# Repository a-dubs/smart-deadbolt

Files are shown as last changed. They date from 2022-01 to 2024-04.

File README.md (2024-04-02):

# Custom Smart Deadbolt 

Brainstormed, designed, built, and programmed a smart deadbolt from scratch

<br>

## Summary
- Attaches to my backdoor’s OEM deadbolt and turns the deadbolt lever to lock and unlock door
  - Mounts to the door and deadbolt without any adhesive or mounting hardware that could potentially damage the door
- Leverages radio modules for communication with smart home controller 
- Powered by an Arduino Pro Mini 5v that drives a high torque TT motor 
- Comprised of 13 different 3D-printed parts
  - Designed from scratch in Autodesk Inventor and 3D printed by yours truly
  - Custom modular design allows for rapid prototyping and iterative design 
- The deadbolt lever has a 3D-printed adapter that snaps around it (no adhesive necesssary) to convert it into one big gear 
  - This gear is then turned by the TT motor through a smaller gear with half the teeth which  
- Limit switch senses when door is closed or open - useful for functionality such as preventing deadbolt from being extended when trying to shut door
- Potentiometer sitting opposite the motor shaft provides two-fold functionality: 
  - Acts as an axle of sorts for the gear driven by the TT motor
  - Is a highly precise, non-volatile, axle "encoder" that allows for knowing the position of the deadbolt gear, and can thus infer when the deadbolt is turned into the unlocked or locked position
- Seamlessly integrates with my custom smart home ecosystem
- Functionality provided by Smart Home:
  - Automatically locks deadbolt after a minute if it is left unlocked
  - Remote monitoring of whether door is ajar/open
  - Remote monitoring and control of the deadbolt from anywhere, enabling the ability to let guests into home remotely
  - Function that prevents deadbolt from locking for any reason - useful for when you want to step outside quickly without needing your keys or a smartphone 
- Currently on its **4th** major version (V4)
  - V1 was the proof of concept
  - V2 was a more complete prototype, with only small improvements over V2, mostly just improved modularity 
  - V3 saw the complete overhaul of the design into a proper enclosure with better modularity and better complexity
  - V4 took V3's complete design and cleaned up the aesthetics considerably, while adding fully realized modularity allowing for the addition of more attachments and sensors

<br>

## Image Gallery

### The Smart Deadbolt w/ Clear Window On
The Smart Deadbolt w/ Clear Window On
<br>

### The Smart Deadbolt in Action!
The Smart Deadbolt in Action
<br>

### 3D Model of Full Assembly (V4) - Clear Walls
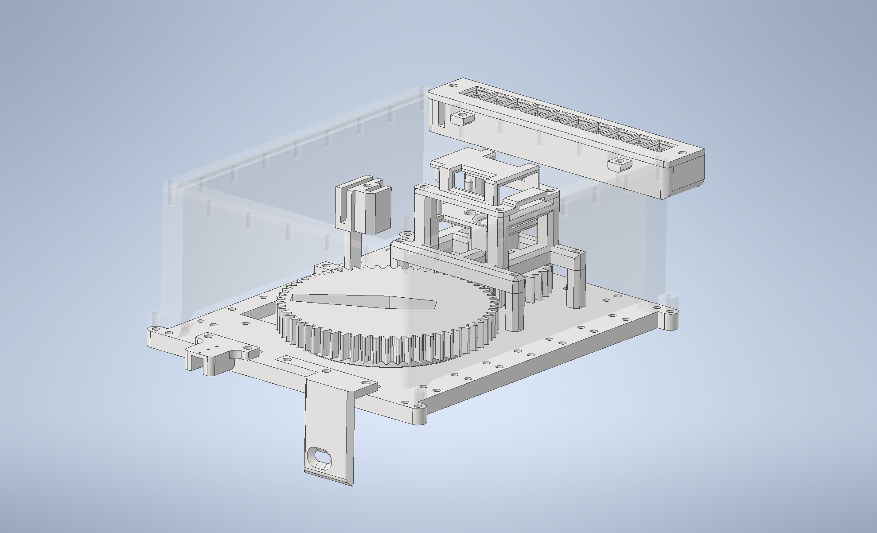
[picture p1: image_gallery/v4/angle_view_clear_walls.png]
3D Model of Full Assembly (V4) - Clear Walls

<br>

### 3D Model of Full Assembly (V4) - Opaque Walls
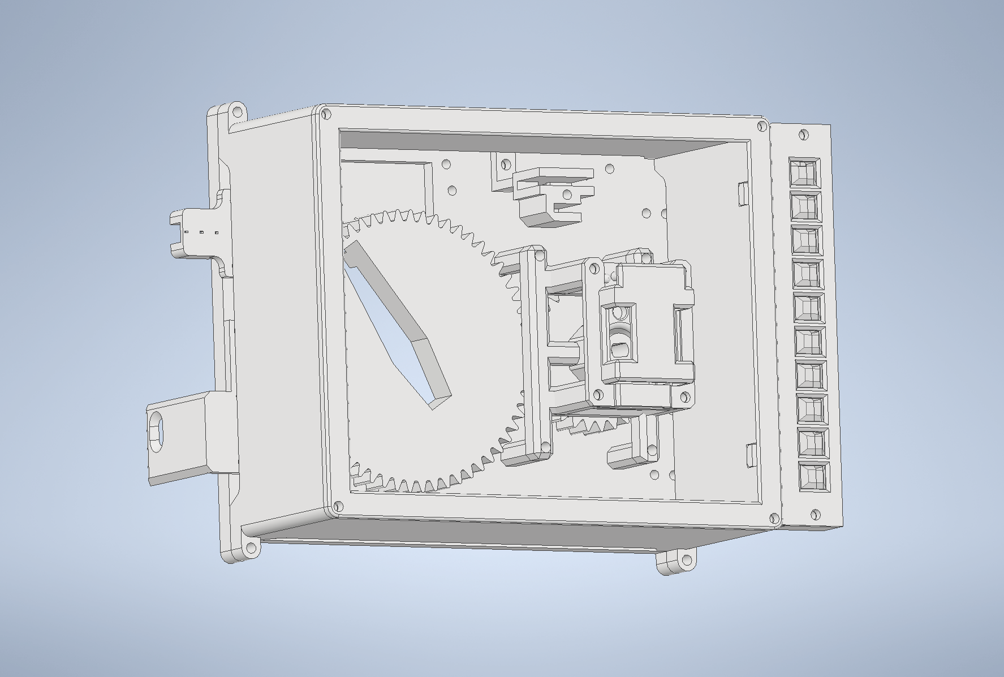
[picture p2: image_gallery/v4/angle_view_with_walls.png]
3D Model of Full Assembly (V4) - Opaque Walls

<br>

### 3D Model of Full Assembly (V4) - Front View
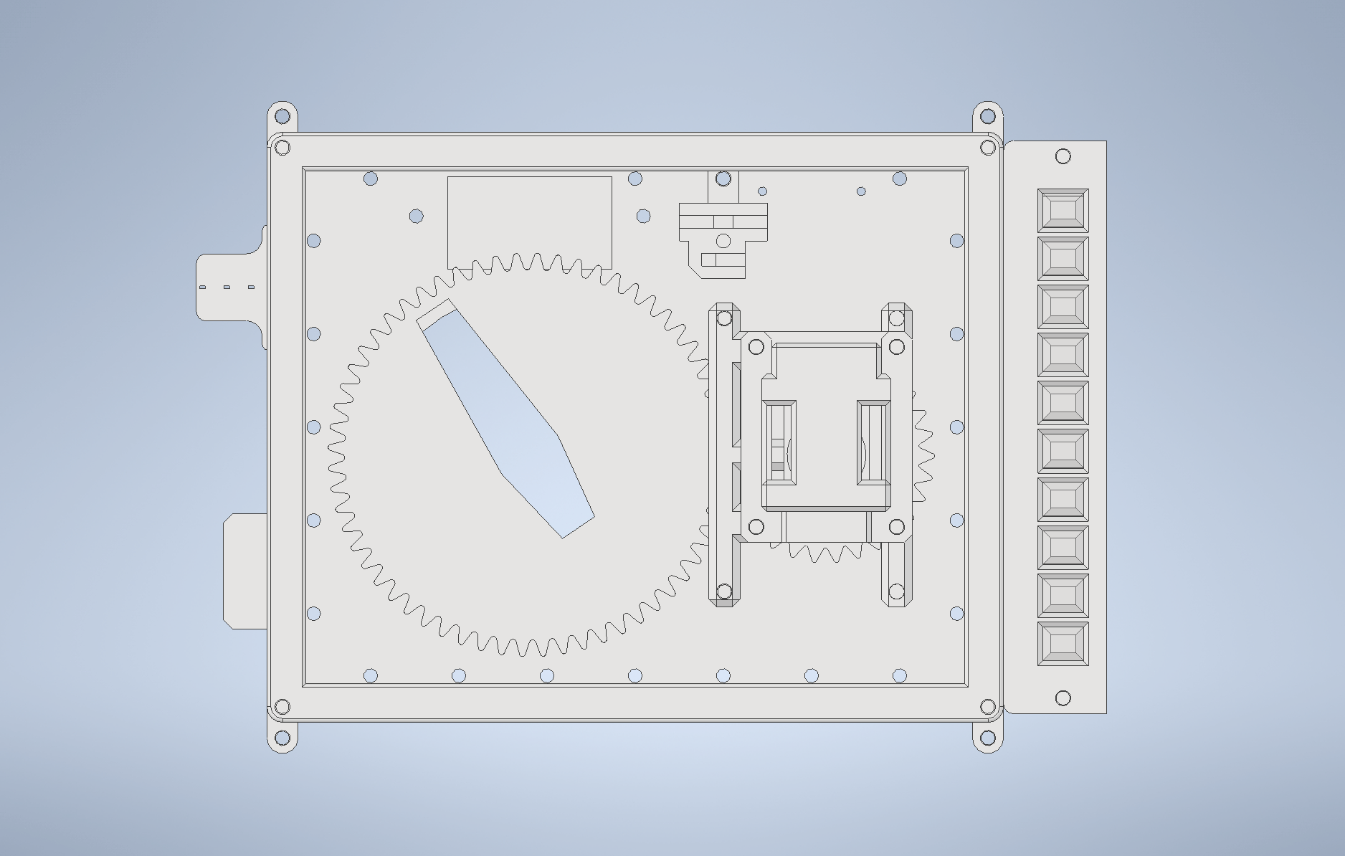
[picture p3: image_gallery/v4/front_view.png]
3D Model of Full Assembly (V4) - Front View

<br>

### OLDER VERSION (V3) - Exploded View of 3D Models 
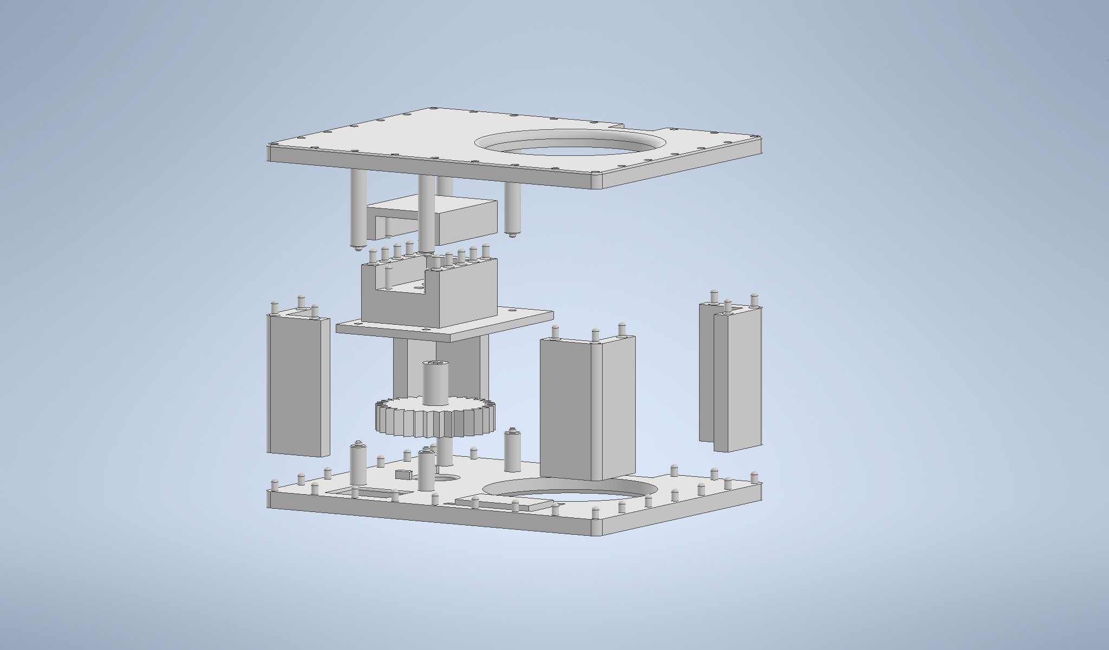
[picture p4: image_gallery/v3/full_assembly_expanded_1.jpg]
OLDER VERSION (V3) - Exploded View of 3D Models

<br>

<!--### Assembly of 3D Printed Components
![assembly of 3d printed components](https://github.com/a-dubs/smart-deadbolt/blob/master/image_gallery/full_assembly_1.jpg)

<br>

### Assembly of 3D Printed Components
![assembly of 3d printed components](https://github.com/a-dubs/smart-deadbolt/blob/master/image_gallery/full_assembly_2.jpg)

<br>

### View w/ Clear Sides
![view with clear sides](https://github.com/a-dubs/smart-deadbolt/blob/master/image_gallery/full_assembly_clear_sides_1.jpg)

<br>

### Exploded View
![exploded view](https://github.com/a-dubs/smart-deadbolt/blob/master/image_gallery/full_assembly_expanded_1.jpg)

<br>

### Exploded View w/ Clear Sides & Bottom
![exploded view with clears sides and bottom](https://github.com/a-dubs/smart-deadbolt/blob/master/image_gallery/full_assembly_expanded_2.jpg)

<br> -->

<br>

## Project Metadata

**Project Status** : Archived  
**Project Progress** : Functional  
**Project Dates** : Oct '21 - Aug '23  

<!-- portfolio.alecwarren.com position priority = 9 (-1 is lowest, 0 is default, 10 is highest) -->

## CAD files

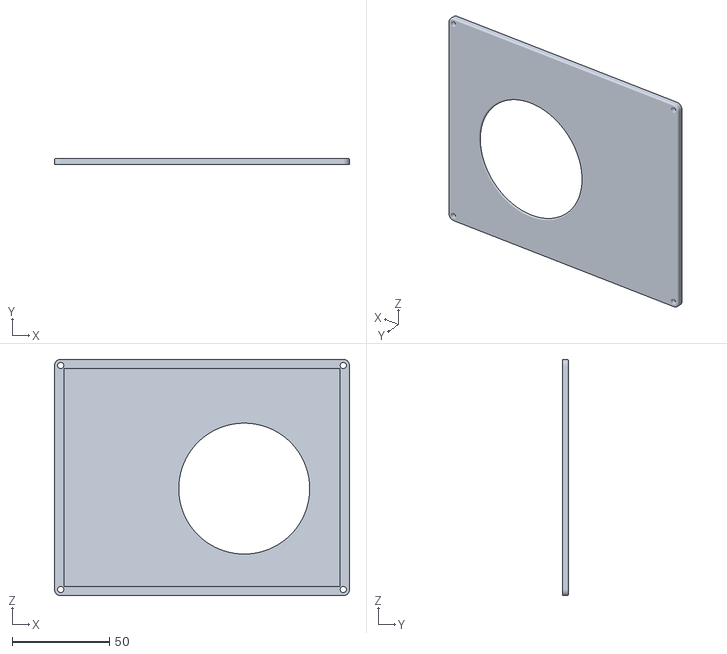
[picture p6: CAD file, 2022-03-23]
3D Modelling/door top plate with full window cutout.stl
151.5 x 3.20 x 121.4

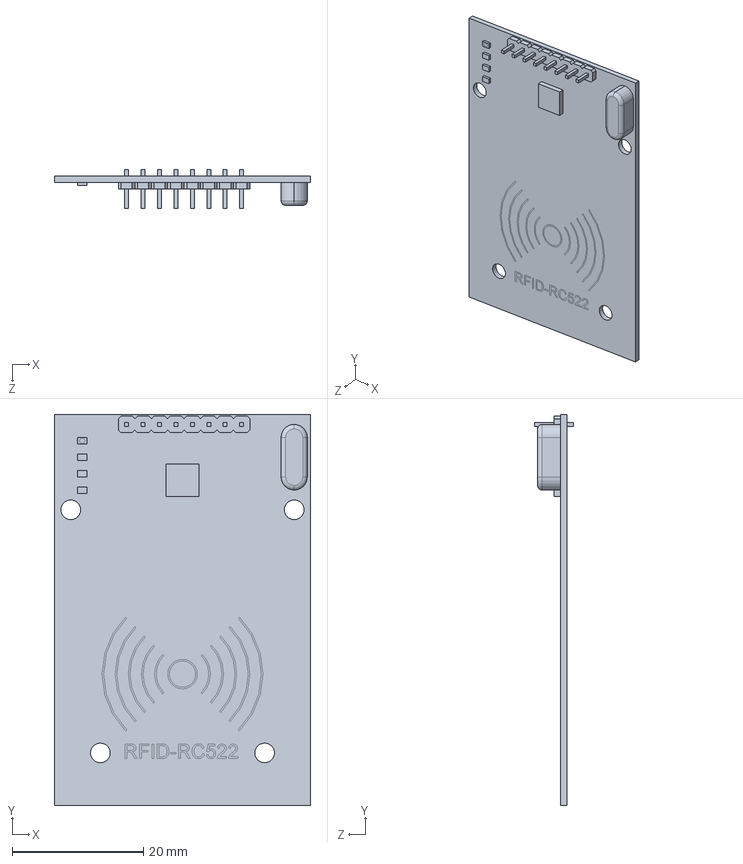
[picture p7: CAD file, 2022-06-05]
3D Modelling/downloaded/RFID-RC522 simple.SLDPRT
39.0 x 59.5 x 6.00 mm

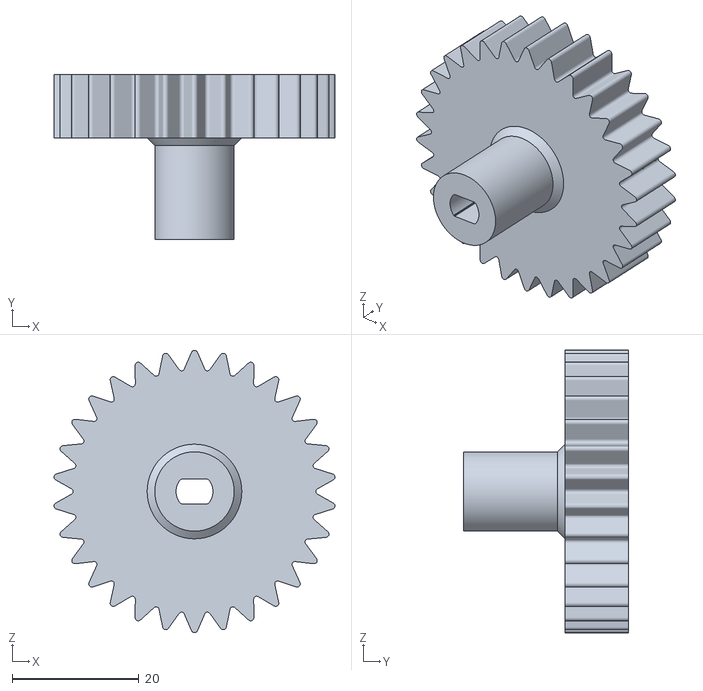
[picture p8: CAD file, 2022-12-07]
3D Modelling/motor gear.stl
44.3 x 26.0 x 44.5

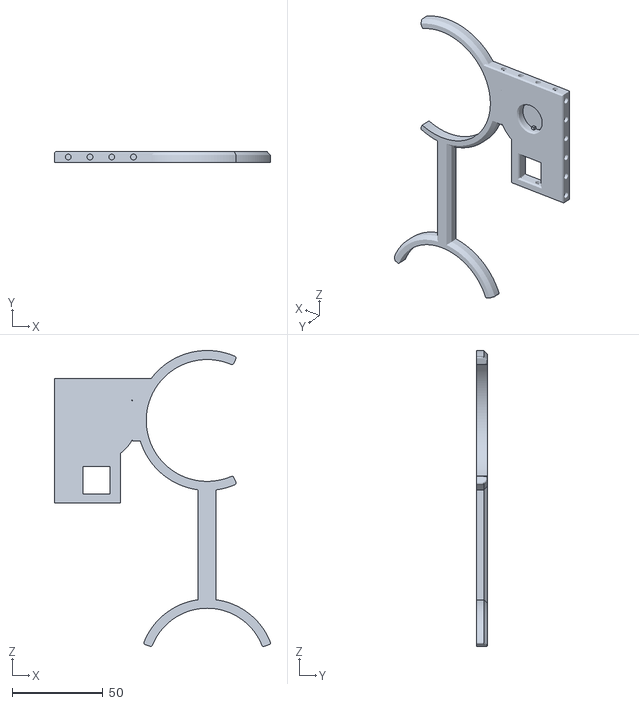
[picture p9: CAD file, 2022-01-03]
3D Modelling/proof of concepts (v1 - v2)/backplate with potentiometer.stl
119.2 x 6.00 x 163.3

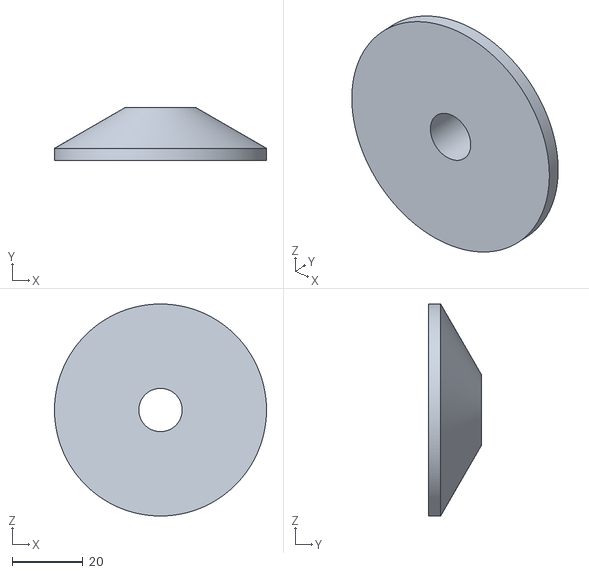
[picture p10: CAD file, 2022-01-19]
3D Modelling/proof of concepts (v1 - v2)/duplicate/driven gear addon.stl
60.0 x 15.0 x 60.0

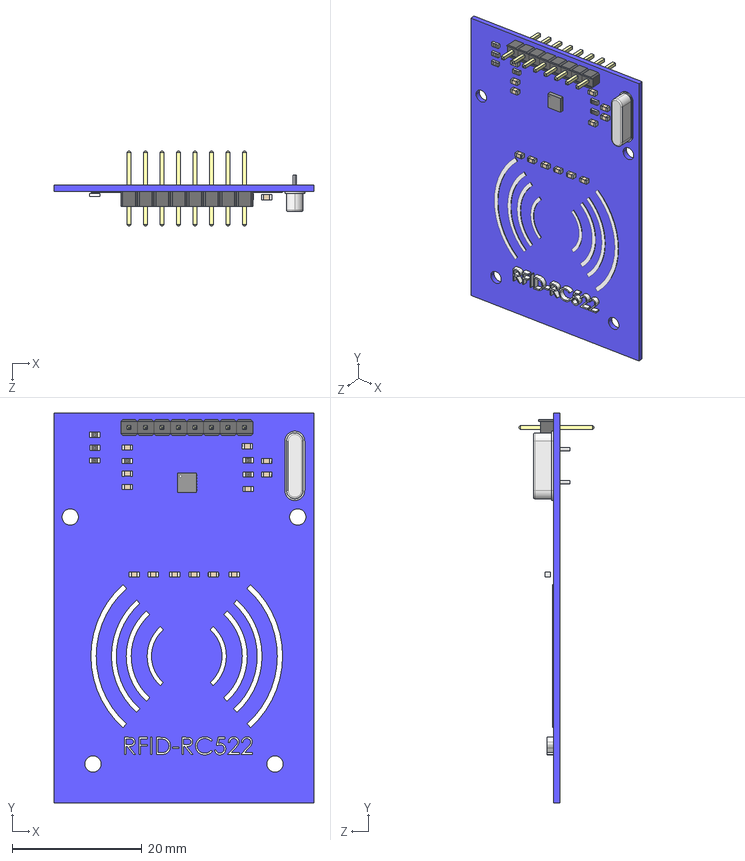
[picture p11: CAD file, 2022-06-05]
3D Modelling/downloaded/RFID.STEP
40.0 x 60.0 x 11.5 mm
User Library-S-PWSON-N12
User Library-Header_Male_8Pin
User Library-SMD Ceramic Capacitors_0603 (1608)_CH x 13

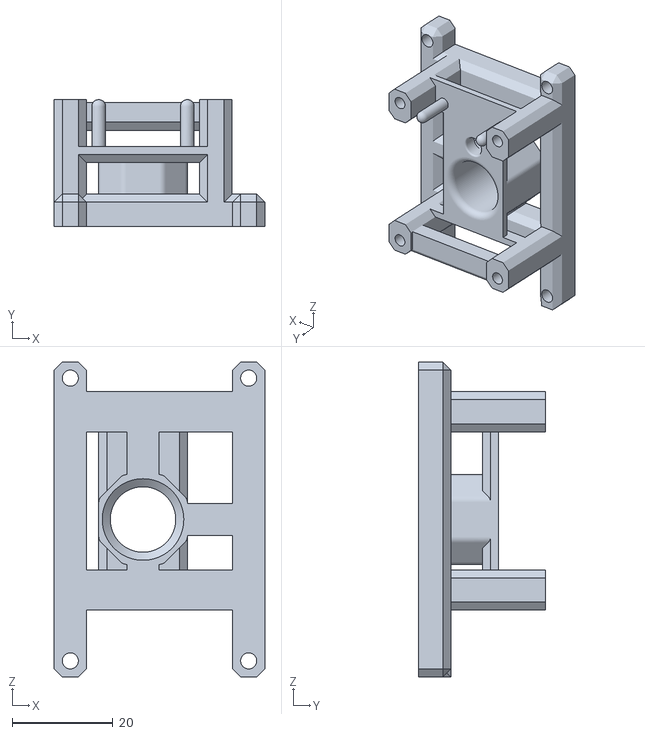
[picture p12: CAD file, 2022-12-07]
3D Modelling/motor mount plate.stl
41.9 x 25.2 x 62.6

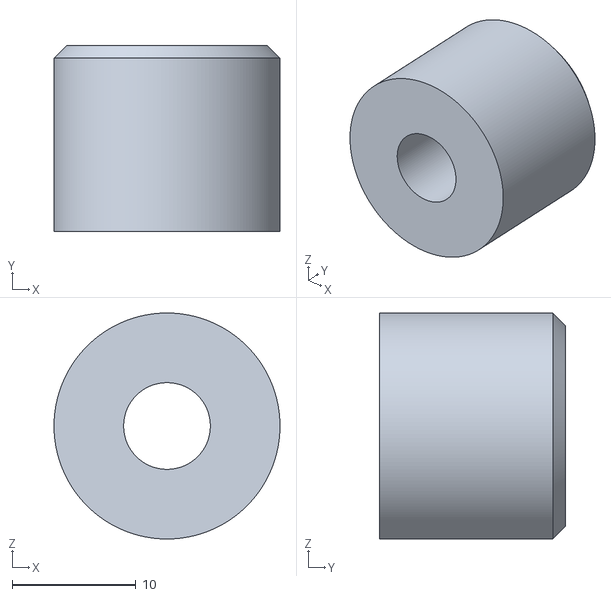
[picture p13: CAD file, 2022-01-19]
3D Modelling/proof of concepts (v1 - v2)/duplicate/driven gear spacer.stl
18.2 x 15.0 x 18.2

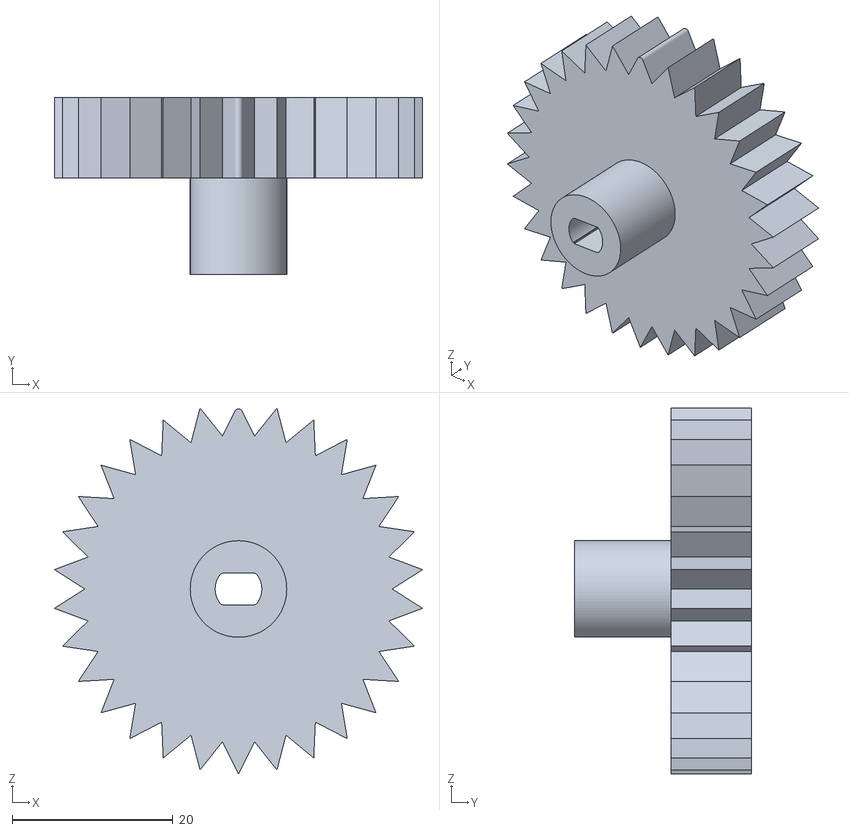
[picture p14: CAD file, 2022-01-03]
3D Modelling/proof of concepts (v1 - v2)/motor driven gear straight teeth for potentiometer.stl
45.7 x 22.0 x 45.5

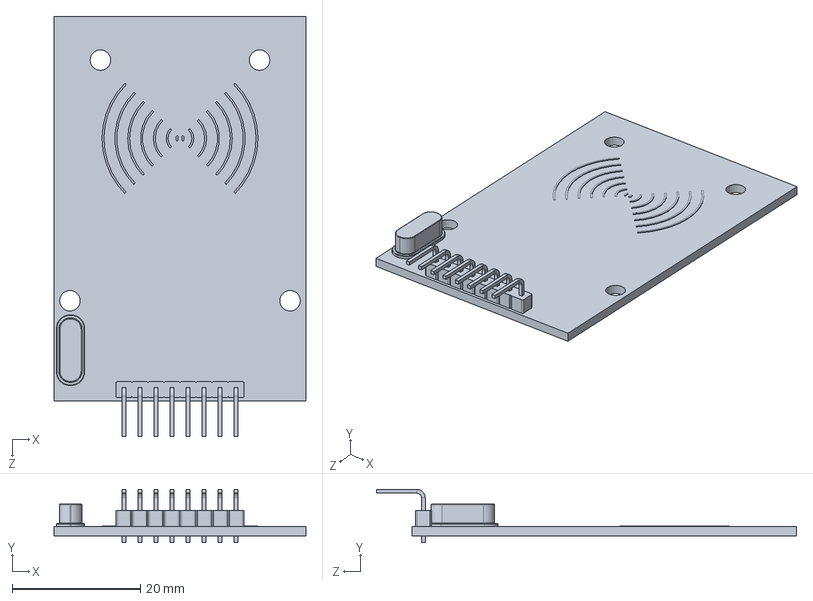
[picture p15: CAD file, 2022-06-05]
3D Modelling/downloaded/RC522.SLDPRT
39.2 x 8.30 x 65.5 mm

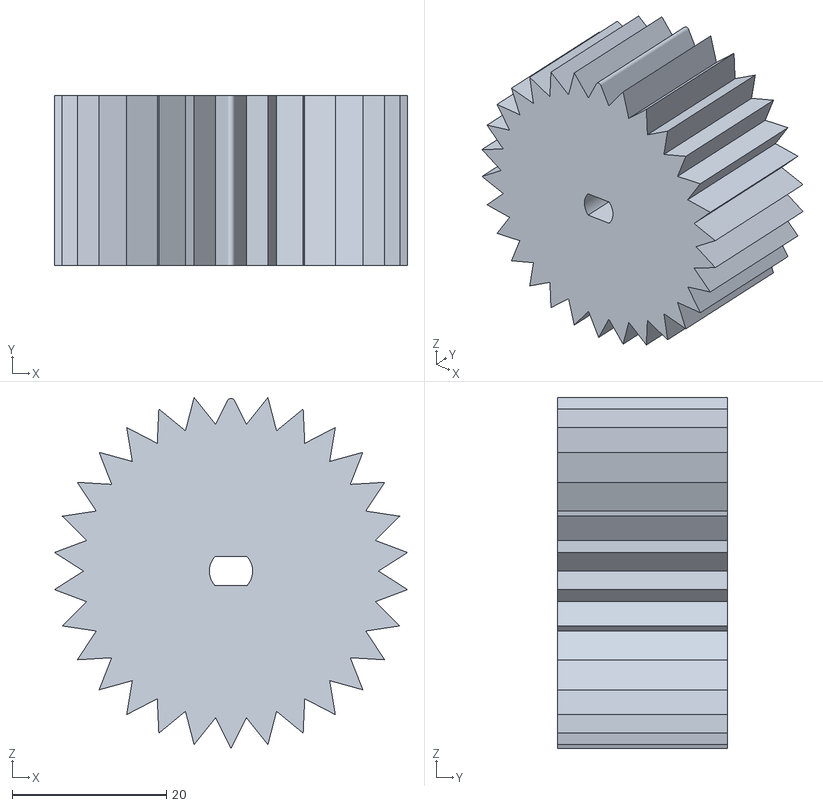
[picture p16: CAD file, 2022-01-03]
3D Modelling/proof of concepts (v1 - v2)/motor driven gear straight teeth for potentiometer tall.stl
45.7 x 22.0 x 45.5

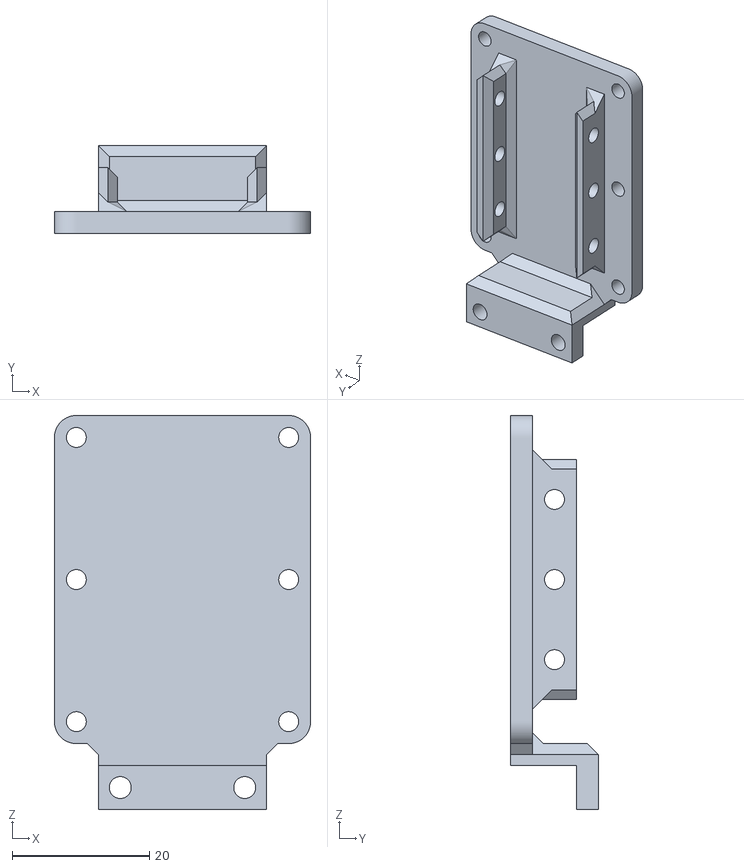
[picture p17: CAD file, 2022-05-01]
3D Modelling/auth arduino mount backplate.stl
37.3 x 12.8 x 57.4

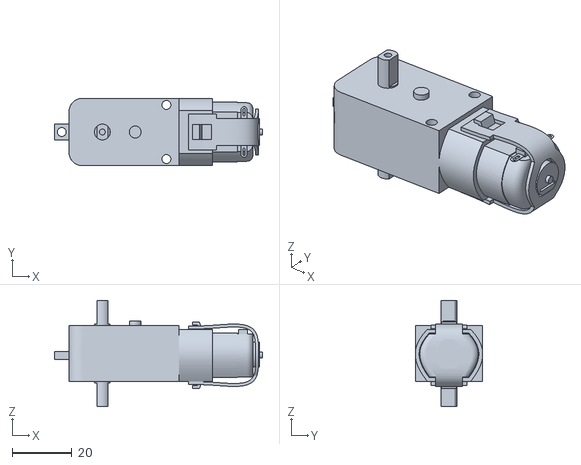
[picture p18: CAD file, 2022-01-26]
3D Modelling/downloaded/Yellow_Motor_Body.stl
69.7 x 22.6 x 35.6

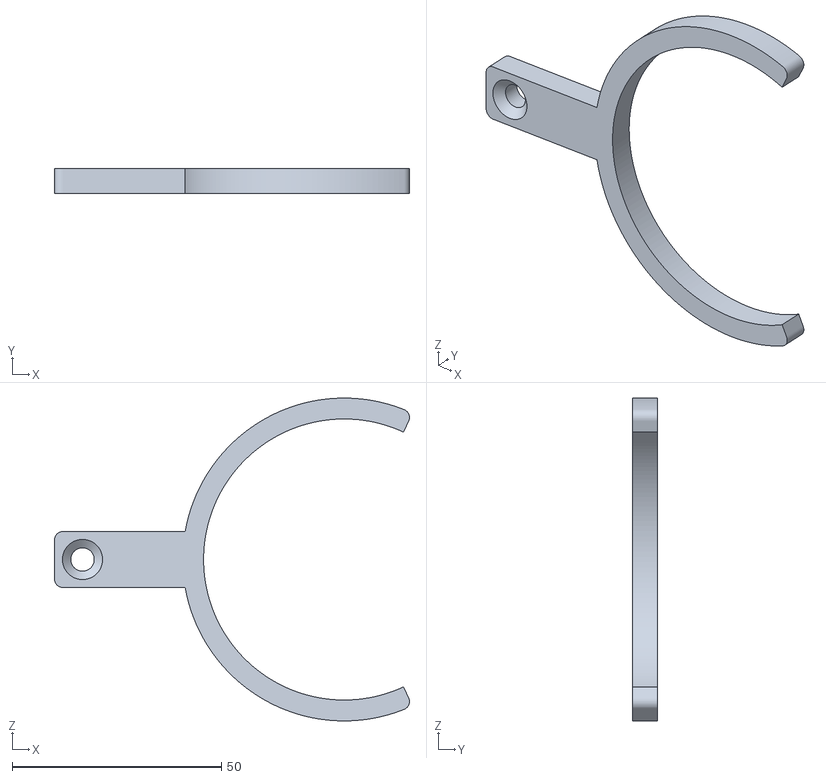
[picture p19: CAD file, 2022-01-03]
3D Modelling/proof of concepts (v1 - v2)/testing gear distances.stl
84.9 x 6.00 x 77.2

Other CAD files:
3D Modelling/power and ground splitter holders.stl
3D Modelling/proof of concepts (v1 - v2)/test attatchment.stl
3D Modelling/proof of concepts (v1 - v2)/backplate reinforcementipt.stl
3D Modelling/10x led strip grid divider opaque.stl
3D Modelling/10x led strip diffuser.ipt
3D Modelling/10x led strip grid divider opaque.ipt
3D Modelling/10x led strip holder .ipt
3D Modelling/10x led strip holder .stl
3D Modelling/10x led strip holder top cover.ipt
3D Modelling/10x led strip holder top cover.stl
3D Modelling/1x led strip diffuser.ipt
3D Modelling/1x led strip diffuser.stl
3D Modelling/OldVersions/10x led strip diffuser.0003.ipt
3D Modelling/OldVersions/10x led strip grid divider opaque.0005.ipt
3D Modelling/OldVersions/10x led strip holder .0009.ipt
3D Modelling/OldVersions/10x led strip holder top cover.0004.ipt
3D Modelling/OldVersions/1x led strip diffuser.0002.ipt
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

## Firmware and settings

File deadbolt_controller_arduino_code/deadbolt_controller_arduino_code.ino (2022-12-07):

#include <LibPrintf.h>
#include <Bounce2.h>
// #inc lude <SharpIR.h>
#include <FastLED.h>

#include <SoftwareSerial.h>

#undef RFID_ENABLED

#ifdef RFID_ENABLED
#include <SPI.h>
#include <MFRC522.h>
#endif
////////////////////////////////////////////////////////////////////////////////////////////////////
//////////////////////////////// Arduino Pro Mini Pinout Resrvations ///////////////////////////////
////////////////////////////////////////////////////////////////////////////////////////////////////

// [ TX   ]   Pin 0  -
// [ RX   ]   Pin 1  -
// [ INT  ]   Pin 2  - Limit Switch Digital Input
// [ INT  ] ~ Pin 3  - Deadbolt Toggle Button Digital Input
// [      ]   Pin 4  - 
// [      ] ~ Pin 5  - 
// [      ] ~ Pin 6  - 
// [      ]   Pin 7  - RF24 CE
// [      ]   Pin 8  - RF24 CS
// [      ] ~ Pin 9  - LED Strip Data Pin
// [ SS   ] ~ Pin 10 - 
// [ MOSI ] ~ Pin 11 - RF24
// [ MISO ]   Pin 12 - RF24
// [ SCK  ]   Pin 13 - RF24
// [      ]   Pin A0 - Motor Forward Digital Output
// [      ]   Pin A1 - Motor Backward Digital Output
// [      ]   Pin A2 - Motor Driver Sleep Digital Output (HIGH = Enable)
// [      ]   Pin A3 - Potentiometer Analog Input
// [      ]   Pin A4 - Ultrasonic Distance Sensor TRIG
// [      ]   Pin A5 - Ultrasonic Distance Sensor ECHO
// [      ]   Pin A6 -
// [      ]   Pin A7 -

#define MOTOR_FORWARD A0
#define MOTOR_BACKWARD A1
#define GEAR_POT A3
#define MOTOR_SLEEP A2
#define DOOR_LIMIT_SWITCH 2
// #define IR_DISTANCE_SENSOR
#define DEADBOLT_TOGGLE_BUTTON 3
#define ULTRASONIC_TRIG A4
#define ULTRASONIC_ECHO A5
#define LED_STRIP_DATA 9
#define MY_RF24_CE_PIN 7
#define MY_RF24_CS_PIN 8

////////////////////////////////////////////////////////////////////////////////////////////////////
////////////////////////////////////////////////////////////////////////////////////////////////////
////////////////////////////////////////////////////////////////////////////////////////////////////

//////////// MY SENSORS STUFF /////////////
// https://www.mysensors.org/download/sensor_api_20
// Enable debug prints
// #define MY_DEBUG
//#define MY_NODE_ID  2


// Enable and select radio type attached
#define MY_RADIO_RF24

#include <MySensors.h>

// MySensors Sensor & Actuator IDs
#define DEADBOLT_ID 30           // ID of the deadbolt actuator that unlocks/locks door
#define MOTDET_ID 31             // ID of the motion sensor for presence detection in LR
#define DOOR_ID 32               // ID of the door sensor for detecting whether door is ajar / has been opened

#define RFID_ID 37

// #define MOT_DET_PIN 2
// #define PERSON_PRESENT_PIN 5


#define LOCKED 1
#define UNLOCKED 0
#define SETUP_MODE 0
#define ULTRASONIC_TRIALS 1
#define LOCKED_POT_POS 220      // min value potentiometer must read for door to be "locked" (in degrees [0-270])
#define UNLOCKED_POT_POS 40      // max value potentiometer must read for door to be "unlocked" (in degrees [0-270])
#define MOTOR_MIN_OVERSHOOT 5    // how many degrees further than the minimum locked/unlocked potentiometer pos must the motor turn the deadbolt until stopping
#define MOTOR_STALL_TIMEOUT 200  // how many ms motor must be "stalled" for until it is considered officially stalled
#define MOTOR_STALL_DIST 1       // min number of degrees that must be advanced within the motor stall timeout window  for it to be considered officially stalled
#define HAND_PRESENT_MAX_DIST 50 // in cm
#define IR_MOTDET_TO ((unsigned long)60000)
#define HEARTBEAT_INTERVAL 1000              // in ms
#define MANUAL_ASSIST_ACTIVATION_THRESHOLD 5 // how many units out of 1024 potentiometer must turn before deadbolt motion is interpreted as the deadbolt being manually turned (>=)
#define KEEP_UNLOCKED_DUR 15000              // in ms, how long should deadbolt stay unlocked for before auto re-locking after being unlocked
#define DOOR_FULLY_OPEN_MIN_DUR 2000
#define MOTOR_MAX_TIME_ON 1000  // how long the motor can continuously run for before being considered stalled

#define ULTRASONIC_ENABLED false
// Bounce2::Button door_limit_switch_debouncer = Bounce2::Button();
//Bounce2::Button deadbolt_toggle_button = Bounce2::Button();
#ifdef RFID_ENABLED
MFRC522 mfrc522(RFID_SS_PIN, RFID_RST_PIN); // Create MFRC522 instance.
#endif
// SharpIR hand_distance_sensor(GP2Y0 A21YK0F_MODEL_CODE, IR_DISTANCE_SENSOR);

//////////////////////////////////////////////////
///////////////// FAST LED STUFF /////////////////
//////////////////////////////////////////////////

#define NUM_LEDS 8
CRGB leds[NUM_LEDS];
unsigned long leds_times_last_updated[NUM_LEDS];
#define TEMP_LEDS_DUR_ON 2000 

/*  DIAGNOSTIC LED STRIP COLOR CODE MEANINGS
+------------------------+-----------------------+
| Purpose                | Color Codes           |
+------------------------+-----------------------+
| Door State             | Red: Ajar             |
|                        | White: Shut           |
+------------------------+-----------------------+
| Deadbolt Current State | Green: Unlocked       |
|                        | Orange: Locked        |
+------------------------+-----------------------+
| Deadbolt Target State  | Green: Unlocked       |
|                        | Orange: Locked        |
+------------------------+-----------------------+
| Hand Detected          | Blue: Hand Detected   |
|                        | Off: Nothing Detected |
+------------------------+-----------------------+
| Authentication         | Red: RFID             |
|                        | Blue: Fingerprint     |
|                        | Off: None             |
+------------------------+-----------------------+
| Motor Warnings         | Red: Stalled          |
|                        | Off: None             |
+------------------------+-----------------------+
| Motor State            | Cyan: Motor on        |
|                        | Off: Motor off        |
+------------------------+-----------------------+
| Deadbolt Last Trigger  | HASS: Cyan            |
|                        | Auth: Magenta         |
|                        | Button: Red           |
|                        | Hand: Blue            |
+------------------------+-----------------------+
| RESERVED               | N/A                   |
+------------------------+-----------------------+
| RESERVED               | N/A                   |
+------------------------+-----------------------+
*/

#define MY_RED CRGB(255, 0, 0)
#define MY_GREEN CRGB(0, 200, 0)
#define MY_BLUE CRGB(0, 0, 200)
#define MY_CYAN CRGB(0, 200, 255)
#define MY_MAGENTA CRGB(255, 0, 200)
#define MY_ORANGE CRGB(150, 70, 0)
#define MY_WHITE CRGB(255, 255, 255)
#define MY_OFF CRGB(0,0,0)

#define DOOR_AJAR_COLOR MY_RED
#define DOOR_SHUT_COLOR MY_WHITE
#define DB_STATE_UNLOCKED_COLOR MY_GREEN
#define DB_STATE_LOCKED_COLOR MY_ORANGE
#define AUTH_RFID_COLOR MY_RED
#define AUTH_FINGERPRINT_COLOR MY_BLUE
#define AUTH_CONNECTED_COLOR MY_WHITE
#define AUTH_DISCONNECTED_COLOR MY_OFF
#define HAND_DET_COLOR MY_BLUE
#define HAND_NOT_DET_COLOR MY_OFF
#define MOTOR_WARN_STALL_COLOR MY_RED
#define MOTOR_WARN_NONE_COLOR MY_OFF
#define MOTOR_STATE_ON_COLOR MY_CYAN
#define MOTOR_STATE_OFF_COLOR MY_OFF 
#define TRIG_HASS_COLOR MY_CYAN
#define TRIG_AUTH_COLOR MY_MAGENTA
#define TRIG_BUTTON_COLOR MY_RED
#define TRIG_HAND_COLOR MY_BLUE


#define LEDS_DOOR_STATE 0
#define LEDS_DB_C_STATE 1 // CURRENT STATE
#define LEDS_DB_T_STATE 2 // TARGET STATE
#define LEDS_HAND_DET 3
#define LEDS_AUTH 4
#define LEDS_MOTOR_WARN 5
#define LEDS_MOTOR_STATE 6
#define LEDS_DB_LAST_TRIG 7
#define LEDS_RESERVED_1 8
#define LEDS_RESERVED_2 9

bool is_led_persistent[NUM_LEDS] = {
    true,    // LEDS_DOOR_STATE 0
    true,    // LEDS_DB_C_STATE 1 // CURRENT STATE
    true,    // LEDS_DB_T_STATE 2 // TARGET STATE
    true,    // LEDS_HAND_DET 3
    false,    // LEDS_AUTH 4
    false,    // LEDS_MOTOR_WARN 5
    true,    // LEDS_MOTOR_STATE 6
    false    // LEDS_DB_LAST_TRIG 7
    };

void set_led(int led_index, CRGB color)
{
    leds[led_index] = color;
    FastLED.show();
    leds_times_last_updated[led_index] = millis();
}

void check_to_clear_leds()
{
    for (int i=0; i < NUM_LEDS; i++)
    {
        if (!is_led_persistent[i] && leds[i] != MY_OFF && (millis() - leds_times_last_updated[i] > TEMP_LEDS_DUR_ON))
        {
            leds[i] = MY_OFF;
            printf("turned off led at index %d\n", i);
            FastLED.show();
        }
    }
    
}

void set_led_strip(CRGB color)
{
    fill_solid(&(leds[0]), NUM_LEDS, color);
    FastLED.show();
}

//////////////////////////////////////////////////
//////////////////////////////////////////////////
//////////////////////////////////////////////////


unsigned long last_time_heartbeat = 0;
unsigned long last_time_hand_detected = 0;
unsigned long last_time_door_closed = 0;
unsigned long last_time_door_opened = 0;
unsigned long last_time_unlocked = 0;
unsigned long last_time_present = 0;
unsigned long time_motor_started = 0;
unsigned long last_time_pot_advanced = 0;
bool door_was_fully_opened = false;
bool person_present = false;
bool person_present_recent_val = false;
short gear_pot_rot = 0;
short new_gear_pot_rot = 0;
bool deadbolt_current_state = UNLOCKED;
bool deadbolt_target_state = UNLOCKED;
bool motor_on = false;
bool motor_stalled = false;
short gear_pot_val_when_stopped; // value read by potentiometer after deadbolt was finished being moved by motor [0-1024]
short gear_pot_val;
bool main_loop_entered = false;
bool door_open = false;
bool button_pressed = false;
bool door_limit_switch_pressed = false;
bool rfid_accepted = false;
unsigned int hand_distance = 1000; // in cm ; set to high starting value so nothing gets triggered at boot
unsigned long dur;                 // variable for the duration of sound wave travel
bool rfid_unlocking_enabled = true;
static unsigned long last_interrupt_time = 0;
unsigned long interrupt_time = millis();
unsigned long db_btn_press_count = 0;
bool db_toggle_btn_pressed = false;
bool keep_unlocked = false;
bool hass_only_ctrl = false;
bool btn_ctrl_en = true;
bool l_sw_ctrl_en = true; 


#define KEEP_UNLOCKED_ID 20
#define HASS_CTRL_ONLY_ID 21 
#define BTN_CTRL_ENABLED_ID 22
#define L_SW_CTRL_ENABLED_ID 23

MyMessage deadbolt_msg(DEADBOLT_ID, V_LOCK_STATUS);
MyMessage motdet_msg(MOTDET_ID, V_TRIPPED);
MyMessage door_msg(DOOR_ID, V_TRIPPED);
MyMessage keep_unlocked_msg(KEEP_UNLOCKED_ID, V_STATUS);
MyMessage hass_ctrl_only_msg(HASS_CTRL_ONLY_ID, V_STATUS);
MyMessage btn_ctrl_enabled_msg(BTN_CTRL_ENABLED_ID, V_STATUS);
MyMessage l_sw_ctrl_enabled_msg(L_SW_CTRL_ENABLED_ID, V_STATUS);

void before()
{
#ifdef RFID_ENABLED
    // Make sure MFRC is disabled from the SPI bus
    pinMode(RFID_SS_PIN, OUTPUT);
    digitalWrite(RFID_SS_PIN, HIGH);
#endif
}

void presentation()
{
    set_led_strip(MY_OFF);
    // Send the sketch version information to the gateway and Controller
    sendSketchInfo("Backdoor MySensors Node V3", "07-07-22");

    // Register all sensors to gw (they will be created as child devices)
    present(DEADBOLT_ID, S_LOCK);
    present(MOTDET_ID, S_MOTION);
    present(DOOR_ID, S_DOOR);
    present(KEEP_UNLOCKED_ID, S_BINARY);
    present(HASS_CTRL_ONLY_ID, S_BINARY);
    present(BTN_CTRL_ENABLED_ID, S_BINARY);
    present(L_SW_CTRL_ENABLED_ID, S_BINARY);
}

// receive message from Gateway for deadbolt motor
void receive(const MyMessage &msg)
{
    printf("Message received for sensor #%d\n", msg.getSensor());
    if (msg.getType() == V_LOCK_STATUS)
    {
        bool lock_status_recvd = !msg.getBool();  // 1 = unlocked for HASS type lock , so invert it
         printf("Message received for deadbolt!\n");
        // if received LOCK command
        // if (msg.getSensor() == RFID_ID)
        // {
        //   if (!lock_status_recvd) {printf("Access granted has been terminated by HASS!\n");}
        // }
        if (msg.getSensor() == DEADBOLT_ID)
        {
            set_led(LEDS_DB_LAST_TRIG, TRIG_HASS_COLOR);
            if (lock_status_recvd)
            {
                lockDeadbolt();
            }
            else
            {
                unlockDeadbolt();
            }
        }
               
        
    }
    else {
      printf("bool msg recv'd: %d\n", msg.getBool());
      bool bool_recvd = msg.getBool();
      if (msg.getSensor() == KEEP_UNLOCKED_ID) 
            keep_unlocked = bool_recvd;
      else if (msg.getSensor() == HASS_CTRL_ONLY_ID) 
            hass_only_ctrl = bool_recvd;
      else if (msg.getSensor() == BTN_CTRL_ENABLED_ID) 
            btn_ctrl_en = bool_recvd;
      else if (msg.getSensor() == L_SW_CTRL_ENABLED_ID) 
            l_sw_ctrl_en = bool_recvd;
    }
}

void unlockDeadbolt(void)
{
    // if not already unlocked
    //  if (gear_pot_rot > UNLOCKED_POT_POS)
    if (deadbolt_target_state != UNLOCKED || deadbolt_current_state != UNLOCKED)
    {
        // if deadbolt is not currently being unlocked by motor
        if (!motor_on || deadbolt_target_state != UNLOCKED)
        {
            motor_on = true;
            printf("Unlocking Deadbolt...\n");
            digitalWrite(MOTOR_BACKWARD, LOW);
            digitalWrite(MOTOR_FORWARD, HIGH);
            time_motor_started = millis();
            last_time_pot_advanced = millis();
            send(deadbolt_msg.set(deadbolt_target_state ? "0" : "1"));
            set_led(LEDS_MOTOR_STATE, MOTOR_STATE_ON_COLOR);
            set_led(LEDS_DB_T_STATE, DB_STATE_UNLOCKED_COLOR);
            set_led(LEDS_MOTOR_WARN, MOTOR_WARN_NONE_COLOR);
        }
        // make sure that deadbolt target state is updated to proper value
        deadbolt_target_state = UNLOCKED;
        last_time_unlocked = millis();
    }
    // deadbolt is already unlocked
    else
    {
        deadbolt_target_state = UNLOCKED;
        last_time_unlocked = millis();
        printf("unlockDeadbolt(): Deadbolt already unlocked!\n");
        stopDeadbolt();
        //  send(deadbolt_msg.set(deadbolt_target_state?"0":"1"));
    }
    set_led(LEDS_DB_T_STATE, DB_STATE_UNLOCKED_COLOR);
}
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
void loop()
{
    if (!main_loop_entered)
    {
        set_led(LEDS_HAND_DET, HAND_NOT_DET_COLOR);
      
        time_motor_started = millis();
        stopDeadbolt();
        door_limit_switch_pressed = digitalRead(DOOR_LIMIT_SWITCH) == LOW; 
        door_open = !door_limit_switch_pressed;
        // update limit switch debouncer
        //    door_limit_switch_debouncer.update();
        //    door_open = door_limit_switch_debouncer.read() != 0;
        // enable motor controller
        digitalWrite(MOTOR_SLEEP, HIGH);
        Serial.print("\n\n\n< ENTERED MAIN LOOP >\n\n\n");
        main_loop_entered = true;
        send(deadbolt_msg.set(deadbolt_current_state ? "0" : "1"));
        send(motdet_msg.set("0"));

        send(door_msg.set(door_open ? "1" : "0"));

        send( keep_unlocked_msg.set( keep_unlocked ? "1" : "0") );
        send( hass_ctrl_only_msg.set( hass_only_ctrl ? "1" : "0") );
        send( btn_ctrl_enabled_msg.set( btn_ctrl_en ? "1" : "0") );
        send( l_sw_ctrl_enabled_msg.set( l_sw_ctrl_en ? "1" : "0") );
        
    }

    //////////////////////////////////////
    // DEADBOLT CONTROL CODE //
    /////////////////////////////////////
    new_gear_pot_rot = (analogRead(GEAR_POT) * 270.0) / 1024.0;
    if ((deadbolt_target_state == LOCKED && new_gear_pot_rot > gear_pot_rot) || (deadbolt_target_state == UNLOCKED && new_gear_pot_rot < gear_pot_rot))
    {
        last_time_pot_advanced = millis();
    }

    gear_pot_rot = new_gear_pot_rot;
    gear_pot_val = analogRead(GEAR_POT);
    //  printf("gear potentiometer rotation [0-270deg]: %d ; raw value: %d\n", gear_pot_rot, gear_pot_val);
      // if deadbolt has been locked
      if (gear_pot_rot >= LOCKED_POT_POS)
      {
          if (deadbolt_current_state != LOCKED)
          {
              if (deadbolt_current_state == UNLOCKED)
              {
                  printf("Deadbolt is now locked\n");
              }

              deadbolt_current_state = LOCKED;
              stopDeadbolt();
          }
          if (motor_on && deadbolt_target_state == LOCKED)
          {
              stopDeadbolt();
          }
      }
      // if deadbolt has been unlocked
      else if (gear_pot_rot <= UNLOCKED_POT_POS)
      {
          if (deadbolt_current_state != UNLOCKED)
          {
              if (deadbolt_current_state == LOCKED)
              {
                  printf("Deadbolt is now unlocked\n");
                  
              }

              deadbolt_current_state = UNLOCKED;
              stopDeadbolt();
          }
          if (motor_on && deadbolt_target_state == UNLOCKED)
          {
              stopDeadbolt();
          }
      }

      // if motor has stalled
      if (motor_on && (millis() - last_time_pot_advanced >= MOTOR_STALL_TIMEOUT || millis() - time_motor_started > MOTOR_MAX_TIME_ON))
      {
          
          motor_stalled = true;
          set_led(LEDS_MOTOR_WARN, MOTOR_WARN_STALL_COLOR);
//          printf("MOTOR STALLED!\n");
          if (millis() - last_time_pot_advanced >= MOTOR_STALL_TIMEOUT)
          { 
            printf("motor stalled #1\n");
          }
          else if (millis() - time_motor_started > MOTOR_MAX_TIME_ON)
          {
            printf("motor stalled #2\n");
          }
          if (deadbolt_target_state == LOCKED)
          {
              unlockDeadbolt();
          }
          else
          {
              lockDeadbolt();
          }
      }

#ifdef RFID_ENABLED
      // activate rfid reader and run RFID scanner logic
      read_rfid();

      // if valid rfid device/tag presented then unlock the deadbolt
      if (rfid_accepted)
      {
          printf("deadbolt unlocked via RFID \n");
          rfid_accepted = false;
          unlockDeadbolt();
      }
#endif

      // update limit switch debouncer
      //      door_limit_switch_debouncer.update();

      // limit switch's state has changed
      //      if ( door_limit_switch_debouncer.changed() ) {
      //
      //        // if limit switch is NOT "pressed" ( == 0) then door has been opened
      //         door_open = door_limit_switch_debouncer.read() != 0;
      //
      //        // after old wire snapped, using normal closed wire instead now
      ////        door_open = door_limit_switch_debouncer.read() == 0;
      //        digitalWrite(DOOR_OPEN_LED, door_open);
      //        // send updated door state msg
      //        send(door_msg.set(door_open ? "1" : "0"));
      //
      //        // if door has just been opened
      //        if (door_open)
      //        {
      //          printf("Door was just opened!\n");
      //        }
      //        // if door has just been closed
      //        else
      //        {
      //          last_time_door_closed = millis();
      //          printf("Door was just closed!\n");
      //          lockDeadbolt();
      //        }
      //

      //      }


      if (door_limit_switch_pressed == door_open)
      {

          // if limit switch is NOT "pressed" ( == 0) then door has been opened
          door_open = !door_limit_switch_pressed;

          // after old wire snapped, using normal closed wire instead now
          //        door_open = door_limit_switch_debouncer.read() == 0;
          
          // send updated door state msg
          send(door_msg.set(door_open ? "1" : "0"));
          set_led(LEDS_DOOR_STATE, door_open ? DOOR_AJAR_COLOR : DOOR_SHUT_COLOR);
          // if door has just been opened
          if (door_open)
          {
              last_time_door_opened = millis();
              // if (last_time_hand_detected > 1000)
              if (!hass_only_ctrl && l_sw_ctrl_en && deadbolt_target_state == LOCKED && deadbolt_current_state != LOCKED)
              {
                  unlockDeadbolt();
                  set_led(LEDS_DB_LAST_TRIG, TRIG_HASS_COLOR);
              }
              printf("Door was just opened!\n");
          }
          // if door has just been closed
          else
          {
              last_time_door_closed = millis();
              printf("Door was just closed!\n");
              if (!hass_only_ctrl && !keep_unlocked && l_sw_ctrl_en)
              {
              lockDeadbolt();
              }
          }
      }

      
  if (digitalRead(DEADBOLT_TOGGLE_BUTTON) == LOW)
  {
    if(db_toggle_btn_pressed != !digitalRead(DEADBOLT_TOGGLE_BUTTON))
    {
      wait(10);
      if (digitalRead(DEADBOLT_TOGGLE_BUTTON) == LOW)
      {
        db_toggle_btn_pressed =  true; // invert it because its pulled HIGH so LOW means pressed
        printf("db toggle button pressed\n");
        if (!hass_only_ctrl && btn_ctrl_en)
        {
          if (deadbolt_target_state == LOCKED)
          unlockDeadbolt();
          else if(deadbolt_current_state == UNLOCKED)
          lockDeadbolt(); 
          set_led(LEDS_DB_LAST_TRIG, TRIG_BUTTON_COLOR);
        }
      }
    }
  }
  
  else if (db_toggle_btn_pressed == true) {
    wait(10);
    if (digitalRead(DEADBOLT_TOGGLE_BUTTON) == HIGH)
    {
      db_toggle_btn_pressed = false;
    }
  }
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

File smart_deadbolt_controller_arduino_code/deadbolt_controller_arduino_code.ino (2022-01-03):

#include <LibPrintf.h>

#define IR_MOT_DET_PIN 7
#define PERSON_PRESENT_PIN 3
#define RELAY3 10
#define MOTOR_FORWARD A0
#define MOTOR_BACKWARD A1
#define GEAR_POT A3
#define MOTOR_SLEEP A2

#define LOCKED 1
#define UNLOCKED 0

#define SETUP_MODE false

#define LOCKED_POT_POS 210 // min value potentiometer must read for door to be "locked" (in degrees [0-270])
#define UNLOCKED_POT_POS  20 // max value potentiometer must read for door to be "locked" (in degrees [0-270])
#define IR_MOTDET_TO ((unsigned long) 20000)


unsigned long last_time_present = 0;
bool person_present = false;
bool person_present_recent_val = false;
short gear_pot_pos = 0;
bool deadbolt_current_state = false;
bool deadbolt_target_state = true;
bool motor_on = false;

void unlockDeadbolt(void)
{
  deadbolt_target_state = UNLOCKED;
  motor_on = true;
//  printf("Unlocking Deadbolt...\n");
  digitalWrite(MOTOR_BACKWARD, HIGH);
  digitalWrite(MOTOR_FORWARD, LOW);
}


void lockDeadbolt(void)
{
  deadbolt_target_state = LOCKED;
  motor_on = true;
//  printf("Locking Deadbolt...\n");
  digitalWrite(MOTOR_BACKWARD, LOW);
  digitalWrite(MOTOR_FORWARD, HIGH);
}

void stopDeadbolt(void)
{
  motor_on = false;
//  printf("Stopping Deadbolt Motor...\n");
  digitalWrite(MOTOR_BACKWARD, LOW);
  digitalWrite(MOTOR_FORWARD, LOW);
}

void setup() {
  // put your setup code here, to run once:
  pinMode(IR_MOT_DET_PIN, INPUT);
  pinMode(PERSON_PRESENT_PIN, OUTPUT);
  pinMode(MOTOR_FORWARD, OUTPUT);
  pinMode(MOTOR_BACKWARD, OUTPUT);
  pinMode(MOTOR_SLEEP, OUTPUT);
  // init value of gear potentiometer position 

  // enable motor controller
  digitalWrite(MOTOR_SLEEP, HIGH);
  if (!SETUP_MODE)
  {
    attachInterrupt(digitalPinToInterrupt(IR_MOT_DET_PIN), presenceISR, RISING);
  }
  Serial.begin(115200);
}

void loop() {
 
    if (person_present_recent_val != person_present)
    {
      
      person_present ? Serial.println("Person is now present!") : Serial.println("Person is no longer present.");
//      person_present ? unlockDeadbolt() : lockDeadbolt();
    }
    person_present_recent_val = person_present;
    if (millis() - last_time_present > IR_MOTDET_TO)
    {
      person_present = false;
    }
    digitalWrite(PERSON_PRESENT_PIN, person_present);

  gear_pot_pos = (analogRead(GEAR_POT) * 270.0) / 1024.0;

  if (!SETUP_MODE)
  {
    if (gear_pot_pos >= LOCKED_POT_POS)
    {
//      deadbolt_current_state = LOCKED;
      if (deadbolt_current_state != LOCKED)
      {
        if (deadbolt_current_state)
        stopDeadbolt();
        printf("Deadbolt is now locked\n");
        deadbolt_current_state = LOCKED;
      }
    }
    else if (gear_pot_pos <= UNLOCKED_POT_POS)
    {
//      deadbolt_current_state = UNLOCKED;
      if (deadbolt_current_state != UNLOCKED)
      {
        printf("Deadbolt is now unlocked\n");
        deadbolt_current_state = UNLOCKED;
          
        stopDeadbolt();
      }
    }
  //  else if (gear_pot_pos > UNLOCKED_POT_POS && gear_pot_pos < LOCKED_POT_POS){
  ////    if (deadboltCurrentState != MOVING)
  ////    {
  ////      printf("Deadbolt is now moving!\n");
  ////      deadboltCurrentState == MOVING;
  ////    }
  //  }

  }  
//
//  static volatile short new_deadbolt_pot_pos =  (analogRead(GEAR_POT) * 270.0) / 1024.0;
//  if ((new_deadbolt_pot_pos - gear_pot_pos > 1) || (new_deadbolt_pot_pos - gear_pot_pos < -1))
//  {
//    printf("gear potentiometer position [0-270deg] %d:\n", new_deadbolt_pot_pos); 
//  }
//  gear_pot_pos = new_deadbolt_pot_pos;
////  printf("raw potentiometer value [0-1024]: %ld\n", analogRead(GEAR_POT));
// 
//  printf("%d, %d\n", deadboltCurrentState, deadboltTargetState);
//  if (deadboltCurrentState != deadboltTargetState && deadboltCurrentState != MOVING)
//  {
//    if (deadboltTargetState == LOCKED)
//    {
//      lockDeadbolt();
//    }
//    else if (deadboltTargetState == UNLOCKED)
//    {
//      unlockDeadbolt();
//    }
//    else {
//      stopDeadbolt();
//    }
//  }
//
//
//  
  if (Serial.available() > 0)
  {
    char ui = Serial.read();
    if (ui == 's')
    {
      stopDeadbolt();
    }
    else if (ui == 'u')
    {
      unlockDeadbolt();
    }
    else if (ui == 'l')
    {
      lockDeadbolt();
    }
    else if (ui == 'p')
    {
      printf("gear potentiometer position [0-270deg] %d:\n", gear_pot_pos);
    }
    else if (ui == 'd')
    {
      printf("Deadbolt is currently %s!\n", deadbolt_current_state == LOCKED ? "locked" : "unlocked");
      printf("Deadbolt's target state is %s!\n", deadbolt_target_state == LOCKED ? "locked" : "unlocked");
      printf("Deadbolt is currently %s!\n", motor_on == true ? "moving" : "stopped");
    }
  }
  delay(10);
//  
//
//  
//
//
//  
//  
// 
//  

}

void presenceISR(void)
{
 
    Serial.println("Presence detected");
  person_present = true;
  last_time_present = millis();
    digitalWrite(PERSON_PRESENT_PIN, HIGH);
}

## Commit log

2022-01-03 v1.0.0 Merged arduino code & 3d models into repo
    [TT motor attach to linear motion gear adapter.0008.ipt, TT motor attach to linear motion gear adapter.ipt, TT motor attach to linear motion gear adapter.stl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]
2022-01-19 v1.0.1 tweaked top of enclosure and standoffs
    [deadbolt enclosure top with window for deadbolt.0002.ipt, deadbolt enclosure top with window for deadbolt.ipt, deadbolt enclosure top with window for deadbolt.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]
2022-01-24 v3.0.0 fixed B2MCS, widened motor plate standoffs
    [door backplate.0015.ipt, door backplate.0018.ipt, door backplate.ipt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]
2022-01-24 v3.0.1 door backplate unsaved changes caught up
    [door backplate.0018.ipt, door backplate.0019.ipt, door backplate.ipt]
2022-01-26 v3.1.0 finalized all parts for 3d printing
    [Yellow_Motor_Body.stl, deadbolt arm adapter gear straight teeth.ipt, deadbolt arm adapter gear straight teeth.stl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]
2022-01-26 v3.4.0 created fully assembly of all parts
    [full deadbolt controller enclosure assembly.0005.iam, full deadbolt controller enclosure assembly.iam]
2022-01-26 v3.4.1 added screenshots of full assembly
2022-02-12 v3.5.0 Began adding MySensors functionality
    [door backplate.0020.ipt, door backplate.0021.ipt, door backplate.ipt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]
2022-03-02 v3.7.0 Limit switch mount 3d model works
    [limit switch mount.0005.ipt, limit switch mount.ipt, limit switch mount.stl]
2022-03-02 v3.7.1 code now works with limit switch
    - deadbolt wont lock when door is ajar
    - auto locks deadbolt immediately upon door being shut
2022-03-06 v3.8.0 toggle button & IR distance sensor added
    - Untested / unverified
2022-03-23 v3.9.0 redesigned top plate and motor holder
    [Yellow_Motor_Body.ipt, door top plate with full window cutout.stl, door top plate with window.0004.ipt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]
2022-03-31 v3.11.0 code works but RFID reader does not
    the code should work but i think the RF module's SPI blocks out the RFID's
2022-04-07 v4.0.1 3d model protos for ultrasonic sensor
    [door top plate with window.stl, motor holder top.0008.ipt, motor holder top.0009.ipt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]
2022-04-10 v4.0.2 commit before next pt (prototype) changes made
    [deadbolt enclosure reinforcer from doorknob.0002.ipt, deadbolt enclosure reinforcer from doorknob.ipt, deadbolt enclosure reinforcer from doorknob.stl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]
2022-04-13 v4.1.0 added led strip models and code and more
    [deadbolt enclosure reinforcer from doorknob.0002.ipt, deadbolt enclosure reinforcer from doorknob.ipt, deadbolt enclosure reinforcer from doorknob.stl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]
2022-04-20 V4.2.0 Many changes to 3d models in prep for v5
    [10x led strip diffuser.0003.ipt, 10x led strip diffuser.ipt, 10x led strip grid divider opaque.0005.ipt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]
2022-05-01 v4.3.0 Added pin reserves to Auth Arduino code
    - Reserved 8 placeholder pins for the 4x4 keypad
    [auth arduino mount backplate.stl, led strip face plate w label addon.0001.ipt, led strip face plate w label addon.ipt]
2022-06-05 v4.4.0 Auth Panel 3D Designing has begun
    - auth panel 2d layout started - fingerprint, keypad, and 2 reset buttons
    - 4x4 keypad model created
    - waterproof cover for the 4x4 keypad created (needs printed & tested)
    [4x4 keypad flexible cover v2.0003.ipt, 4x4 keypad flexible cover v2.1.ipt, 4x4 keypad flexible cover v2.ipt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]
2022-06-07 v4.4.1 Random progress commit
    [authentication panel.0005.ipt, authentication panel.ipt]
2022-06-07 v4.4.2 added outer magnet & screw cutouts. started adding keypad gasket
    [4x4 keypad flexible cover v2.0003.ipt, 4x4 keypad flexible cover v2.0007.ipt, 4x4 keypad flexible cover v2.ipt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]
2022-06-08 v4.4.3 Started turning auth panel into 3D
    [4x4 keypad flexible cover v2.0007.ipt, 4x4 keypad flexible cover v2.0008.ipt, 4x4 keypad flexible cover v2.ipt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]
2022-06-08 v4.4.4 last commit with all seal holes in place
    [authentication panel.0015.ipt, authentication panel.0016.ipt, authentication panel.ipt]
2022-06-10 v4.4.5 commit before merging changes made offline
    [4x led strip divider.0001.ipt, 4x led strip divider.ipt, auth panel face plate.ipt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]
2022-06-10 v4.5.0 merged offline changes made to auth panel
    [1x3 button cover.ipt, auth panel assembly.iam, auth panel cover.ipt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]
2022-06-12 v4.5.1 before merging 6-11 offline changes
    [1x3 button assembly.0002.iam, 1x3 button assembly.iam, 1x3 button cover.0001.ipt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]
2022-06-15 v4.5.2 committing all recent auth panel changes
    [1x3 button assembly.0006.iam, 1x3 button assembly.iam, 1x3 button cover.ipt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]
2022-07-21 4.6.0 Initial auth panel modelling is almost done
    [auth panel assembly.0008.iam, auth panel assembly.0011.iam, auth panel assembly.iam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]
2022-07-21 v4.7.0 Disabled ultrasonic. used button only
2022-12-07 v4.6.0 Did some tidying on the repo
    [1x3 button assembly.0002.iam, 1x3 button assembly.iam, 1x3 button cover.0001.ipt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]
2022-12-07 v4.7.0 checking in most recent code and 3d models
    [auth panel assembly.0012.iam, deadbolt arm adapter gear straight teeth.0008.ipt, deadbolt arm adapter gear straight teeth.0009.ipt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]
